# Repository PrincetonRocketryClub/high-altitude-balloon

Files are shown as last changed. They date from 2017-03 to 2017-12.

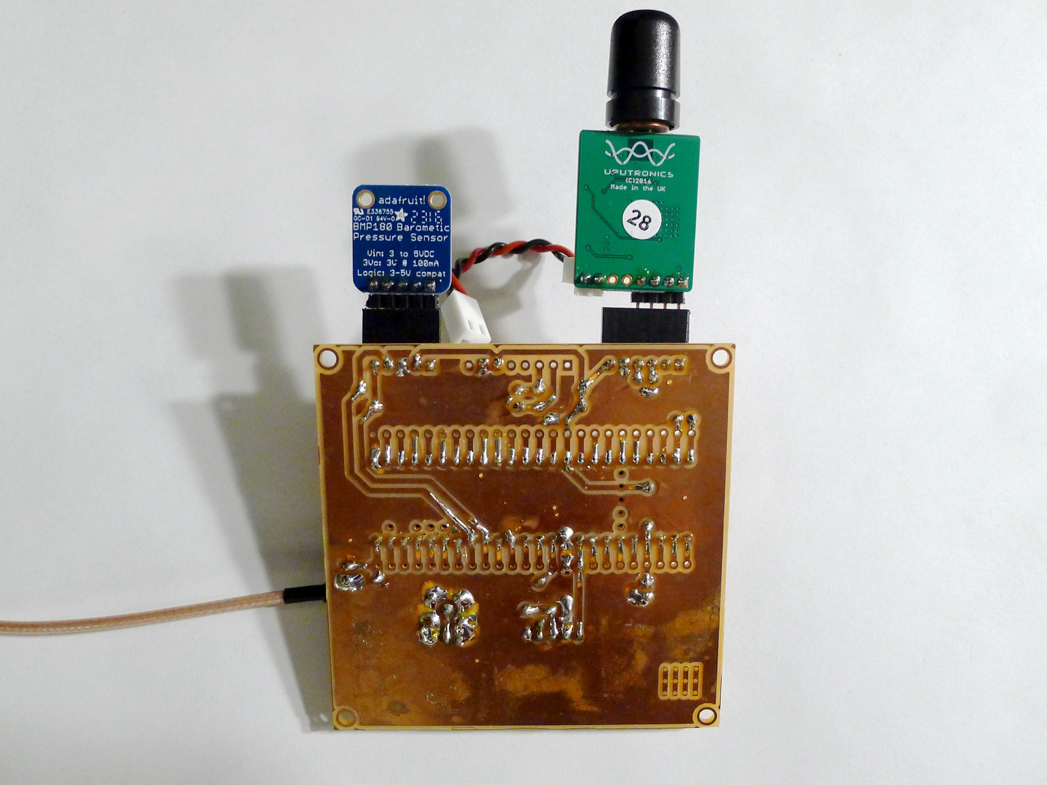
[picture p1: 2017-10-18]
images/avionics_back.jpg

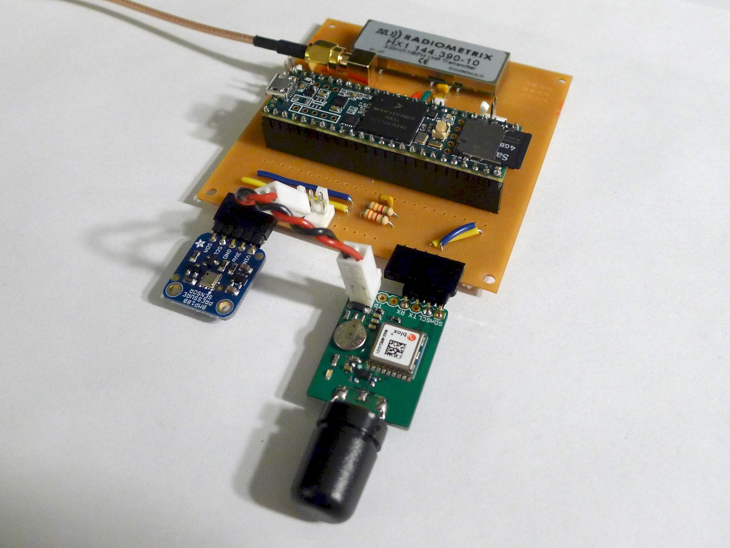
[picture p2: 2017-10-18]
images/avionics_front.jpg

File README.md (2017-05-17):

# High Altitude Balloon
High Altitude Balloon for the Global Space Balloon Challenge.

Electronics without battery is 70 grams, battery is 98 grams.

## Controller
The primary microcontroller used is a [Teensy 3.5](https://www.pjrc.com/store/teensy35.html). The Teensy is a Arduino-compatible ARM based development board. 

Software will be based on the [Trackuino project](https://github.com/trackuino/trackuino) with modifications for Teensy DAC support from [this project.](https://github.com/rvnash/aprs_teensy31)

## Communications
Telemetry will be sent via 2m APRS using the [HX1 2m Transmitter](http://www.radiometrix.com/content/hx1). This module has an output power of ~300mW tuned to a frequency of 144.390 MHz. There are reports of frequency drift with temperature, so this behavior will have to be characterized before launch.

Antenna will be a simple half-wavelength dipole, likely based on [this](http://bear.sbszoo.com/construction/antenna/cf/hwcf2.htm) or [this.](http://bear.sbszoo.com/construction/antenna/cf/hwcf1.htm)

### APRS Message Format
Use standard headers etc. Symbol `/O` (Primay symbol table, symbol ID 'O' corresponding to balloon). Message type based on "Lat/Long Position Report Format — with Data Extension and Timestamp" in the [APRS spec](http://www.aprs.org/doc/APRS101.PDF).

String:
`[Data Type ID flag:/]HHMMSSh[Latitude ddmm.hh[N/S](8b)][SymtableID (1b)][Longitude dddmm.hh[W/E](9b)][Symbol Code (1b)][Course/Speed (7b)][Arb. data (36b)]`  

### Comment format
Chars | Description | Example
----- | ----------- | -------
5 | Timestamp (sec) | 12000
1 | Separator | ,
5 | BMP180 Temperature (C) | -60.0
1 | Separator | ,
6 | BMP180 Pressure (Pa) | 101580
1 | Separator | ,
4 | Thermistor ADC Value, max 1023 | 1017
23 | Total |

### HX-1 Transmitter
- [Main Page](http://www.radiometrix.com/content/hx1)

Pinout

Pin Label | Functionality | Connection
--------- | ------------- | ----------
1, 3 | RF Ground | SMA Shield
2 | RF out | SMA Center pin
4 | Active-high Enable | Digital pin 11
5 | 5V Supply | N/A
6 | GND | N/A
7 | TX Data | DAC1

# Sensors
## U-Blox MAX-M8 GPS Receiver
### Datasheets
- [Breakout Board](https://store.uputronics.com/?route=product/product&product_id=72)
- [Hardware Specs](https://www.u-blox.com/sites/default/files/MAX-M8-FW3_DataSheet_%28UBX-15031506%29.pdf)
- [Protocol Spec](https://www.u-blox.com/sites/default/files/products/documents/u-blox8-M8_ReceiverDescrProtSpec_%28UBX-13003221%29_Public.pdf)

### Software
Outputs NEMA strings over serial, so should integrate with Trackuino's code nicely. Might have to do some configuration via UART. See page 175 of protocol spec for NMEA config. 

Config example code: http://playground.arduino.cc/UBlox/GPS
Other tutorial: http://ava.upuaut.net/?p=738

The settings we'll need:
- Set non-GPS source's ID's to GPGGA for compatibility
- Double check all available sources are enabled
- Disable some unnecessary debug outputs
- Figure out how to switch between low and high altitude mode
- Change refresh rate

### I/O
Pin Label | Functionality | Connection
--------- | ------------- | ----------
SDA | I2C | N/A
SCL | I2C | N/A 
TXD | Serial UART | Serial4 RX
RXD | Serial UART | Serial4 TX
GND | Ground | 
VCC | 3.3V Power | 

## BMP180 Barometer/Temperature
### Datasheets
- [Adafruit](https://www.adafruit.com/products/1603)
- [Library](https://learn.sparkfun.com/tutorials/bmp180-barometric-pressure-sensor-hookup-/installing-the-arduino-library)

### Software
Use the Sparkfun library. Communicates over I2C, nothing fancy. Must use SCL/SDA0 since those correspond to the default Wire interface.

### I/O
Pin Label | Functionality | Connection
--------- | ------------- | ----------
VIN | 5V power in, feeds on-board regulator | N/A
3V3 | 3V3 power rail | N/A 
GND | Ground | Black
SCL | I2C | SCL0 (Pin 19)
SDA | I2C | SDA0 (Pin 18)

## MMA8451 3-axis accelerometer
### Datasheets
- [Adafruit](https://www.adafruit.com/product/2019)
- [Library](https://learn.adafruit.com/adafruit-mma8451-accelerometer-breakout/wiring-and-test)

### Software
Use the Adafruit library. Communicates over I2C.

### I/O
Pin Label | Functionality | Wire Color
--------- | ------------- | ----------
VIN | 5V power in, feeds on-board regulator | NC
3Vo | 3V3 power rail | N/A 
GND | Ground | Black
SCL | I2C | SCL0 (Pin 19)
SDA | I2C | SDA0 (Pin 18)
A | Address Select | NC for address 0x1C
I1 | Interrupt 1 | NC
I2 | Interrupt 2 | NC

## 3950 NTC Thermristor
### Datasheets
- [Adafruit](https://www.adafruit.com/product/372)
- [Tutorial](https://learn.adafruit.com/thermistor/using-a-thermistor)
- [Lookup Table](https://cdn-shop.adafruit.com/datasheets/103_3950_lookuptable.pdf)

Hook it up with a 10k resistor in a voltage divider setup, read with ADC. Connected to ADC17

# Actuators

## Electric heating pad

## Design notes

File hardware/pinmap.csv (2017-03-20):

Teensy Pin | Configuration | Connected To | Wire Color
0
1
2
3
4
5
6
7
8
9
10
11 | Digital Out | HX1 Transmitter Enable
12
13
14
15
16 | SDA0 | Accelerometer, Barometer I2C
17 | SCL0 | Accelerometer, Barometer I2C
18
19
20
21
22
23
24
25
26
27
28
29
30
31 | Serial4 RX | GPS TX
32 | Serial4 TX | GPS RX
33
34 | Analog In 17 | Thermistor
35
36
37
38
39
DAC0
DAC1 |  | HX1 Transmitter Signal

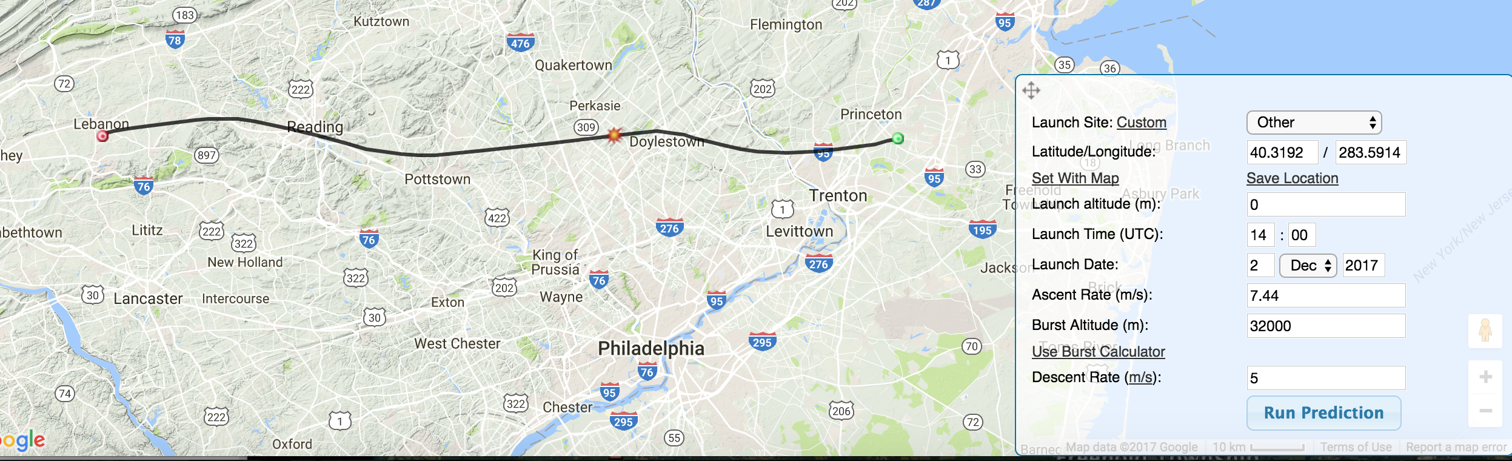
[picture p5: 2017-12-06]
records/Screen Shot 2017-12-01 at 11.11.32 PM.png

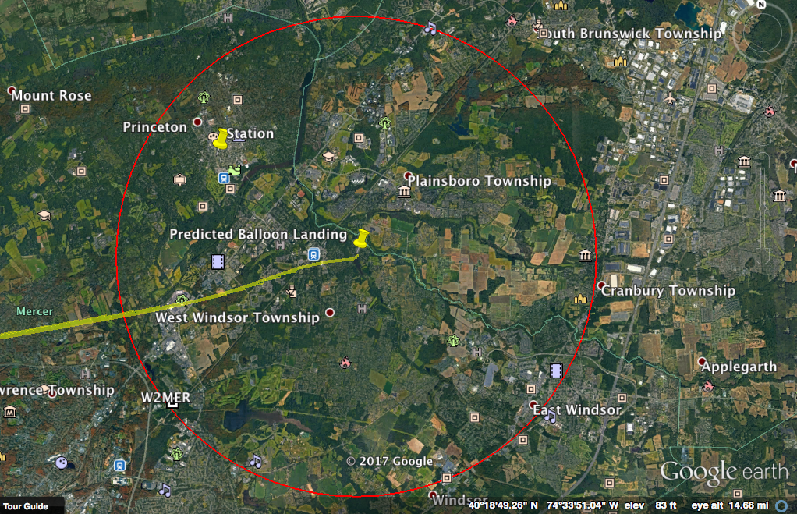
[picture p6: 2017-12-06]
records/Screen Shot 2017-12-01 at 11.14.21 PM.png

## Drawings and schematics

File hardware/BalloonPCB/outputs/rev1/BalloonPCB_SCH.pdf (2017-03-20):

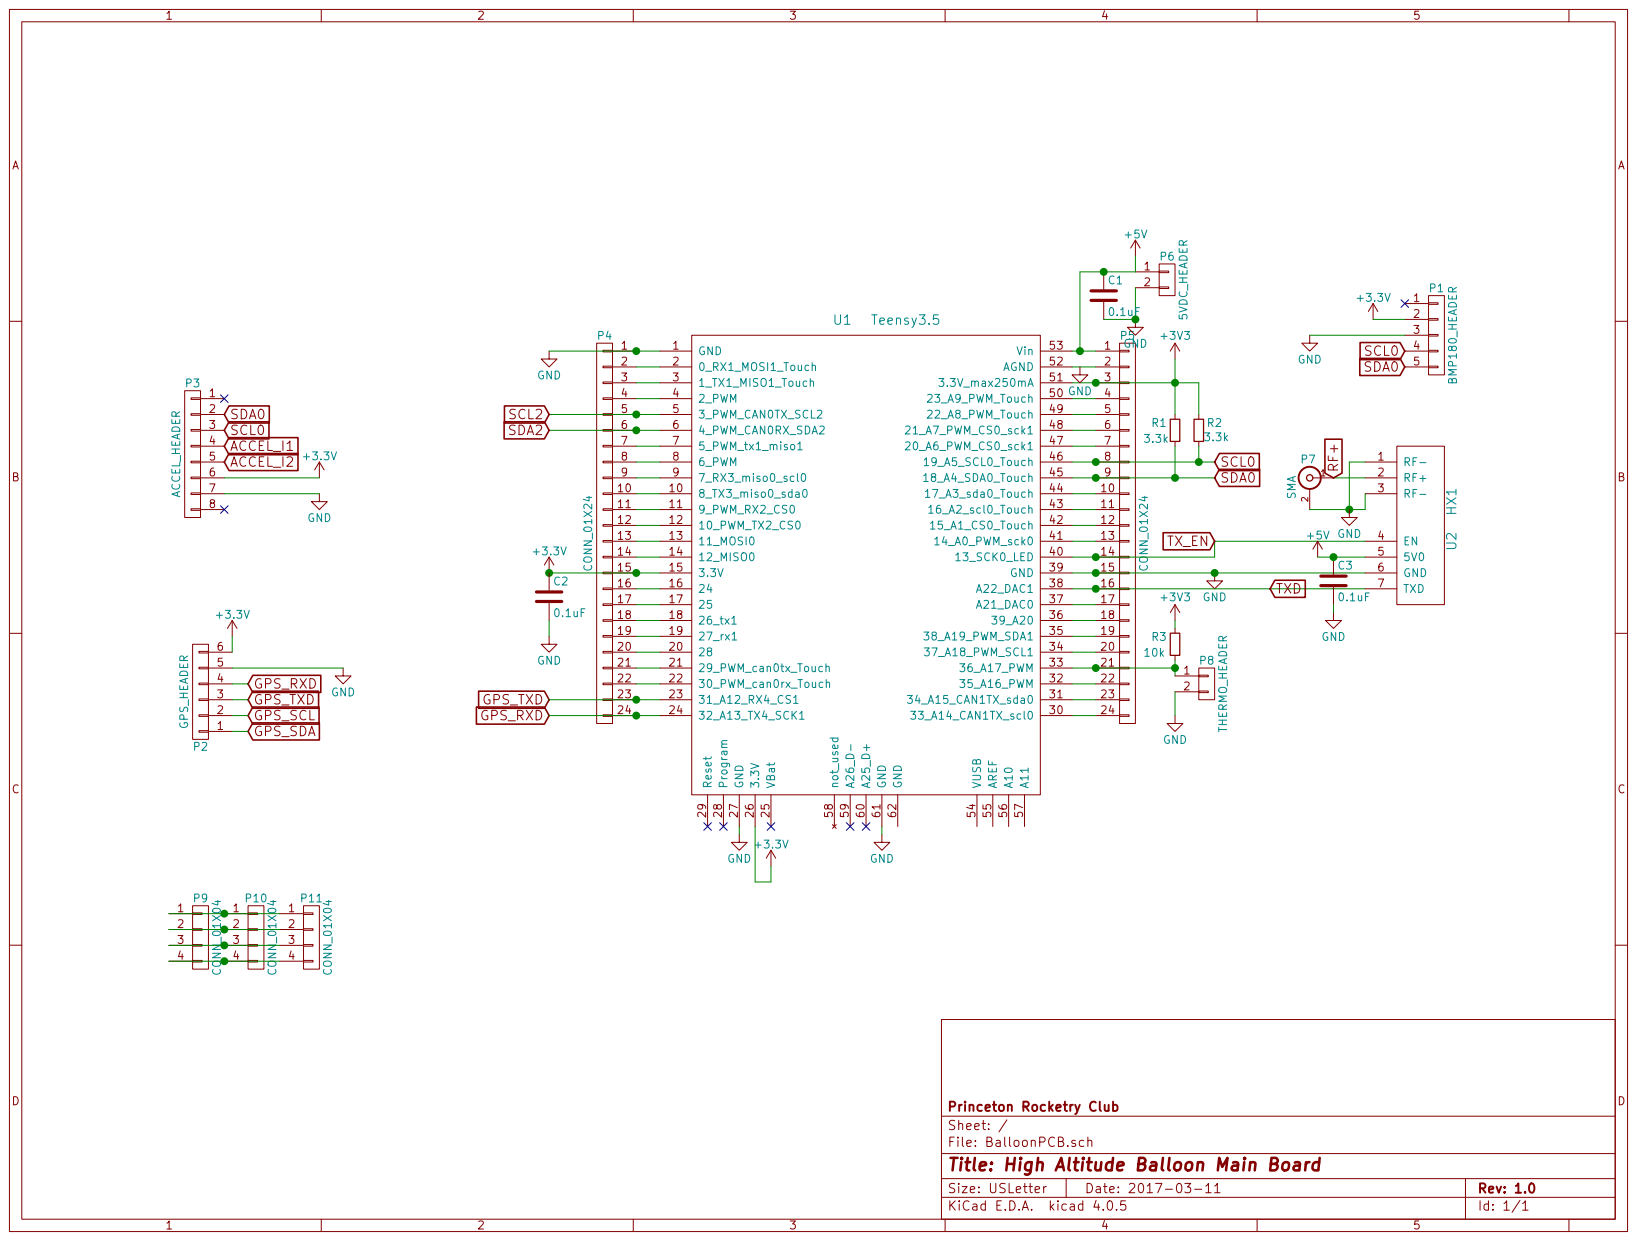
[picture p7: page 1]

2 3 4 5 | 0_RX1_MOSI1_Touch 2 1_TX1_MISO1_Touch 3 2_PWM 4 3_PWM_CAN0TX_SCL2 5 | 2

GND 4

6 | 4_PWM_CAN0RX_SDA2 6 | 6
7 8 9 10 11 12 13 14 15 | 5_PWM_tx1_miso1 7 6_PWM 8 7_RX3_miso0_scl0 9 8_TX3_miso0_sda0 10 9_PWM_RX2_CS0 11 10_PWM_TX2_CS0 12 11_MOSI0 13 12_MISO0 14 3.3V 15 | 7

12
13

16 17 18 19 20 21 22 23 | 24 16 25 17 28 20 29_PWM_can0tx_Touch 21 31_A12_RX4_CS1 23 | 16

17
18
19
20

22
23

24 | 32_A13_TX4_SCK1 24 | 24

Princeton Rocketry Club
Sheet: /
File: BalloonPCB.sch
Title: High Altitude Balloon Main Board

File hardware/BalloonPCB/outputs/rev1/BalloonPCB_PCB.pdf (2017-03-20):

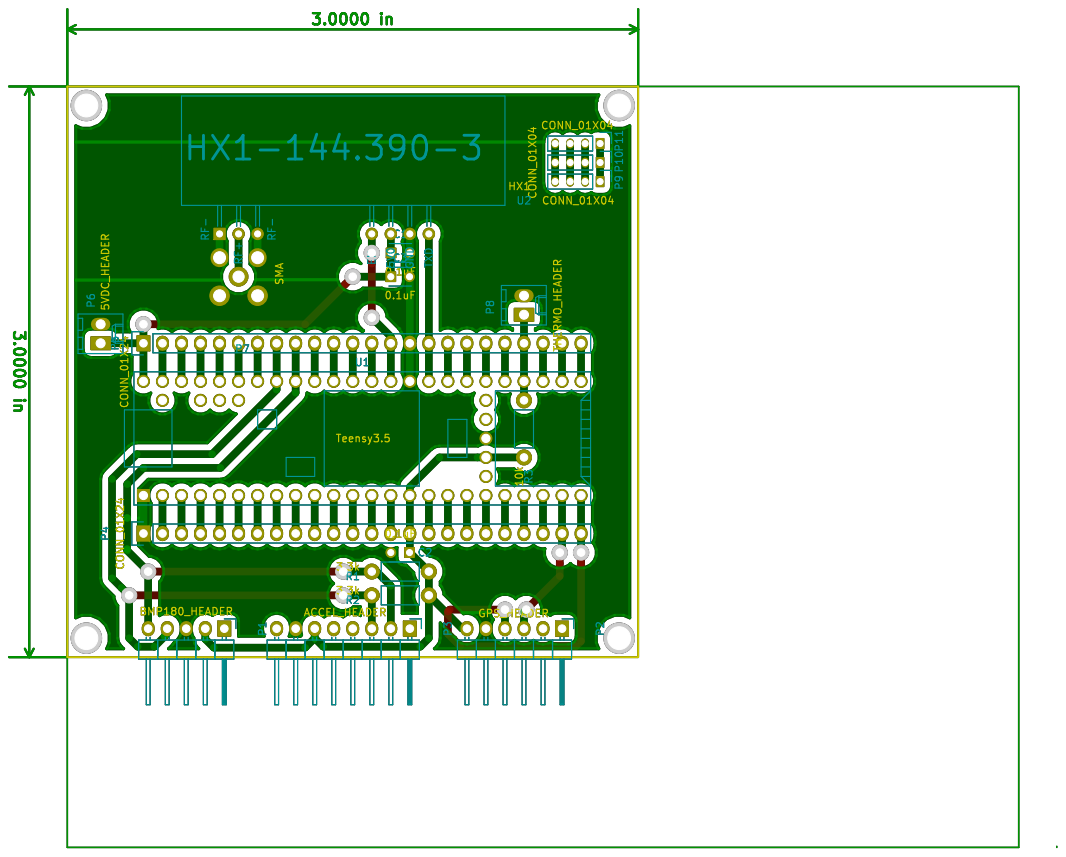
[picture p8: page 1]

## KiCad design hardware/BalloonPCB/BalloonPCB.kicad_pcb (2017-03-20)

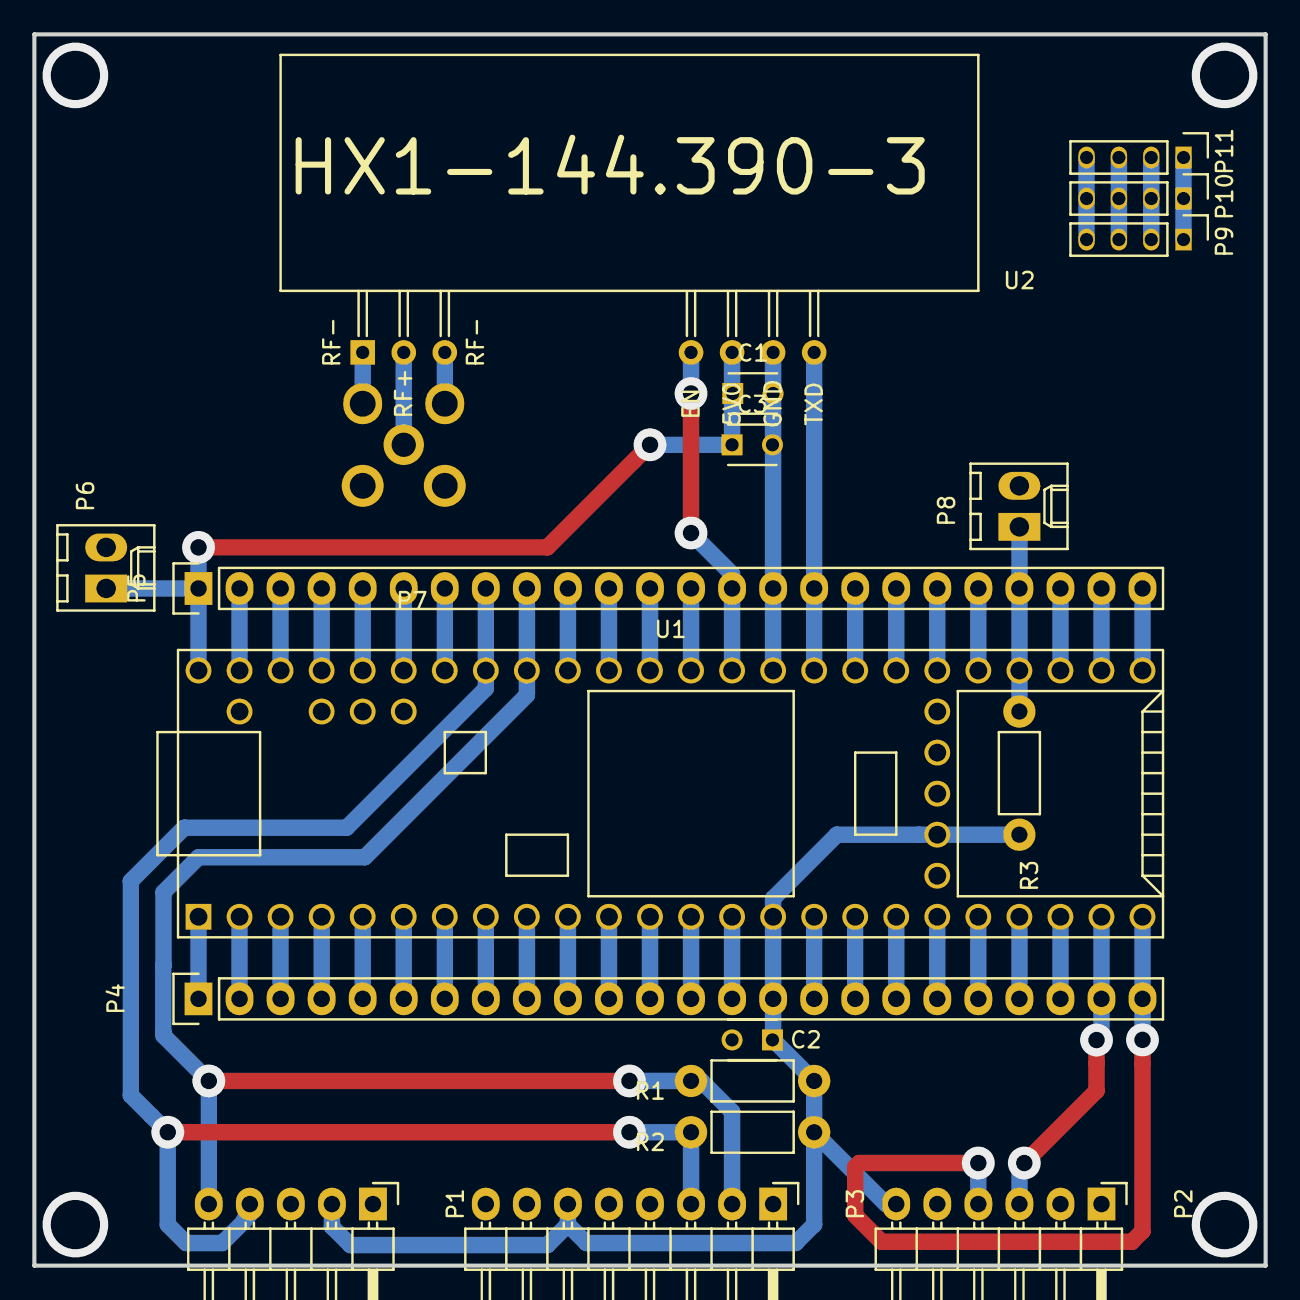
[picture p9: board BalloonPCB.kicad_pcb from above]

Board: 2 copper layers, 76.2 x 76.2 mm, 19 parts (0 on the bottom side), 51 nets.

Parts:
C1, C2, C3: 0.1uF; C_Disc_D3_P2.5
P1: BMP180_HEADER; Pin_Header_Angled_1x05
P2: GPS_HEADER; Pin_Header_Angled_1x06
P3: ACCEL_HEADER; Pin_Header_Angled_1x08
P4, P5: CONN_01X24; Pin_Header_Straight_1x24
P6: 5VDC_HEADER; Molex_KK-6410-02_02x2.54mm_Straight
P7: SMA; SMA_Socket_TYCO-AMP
P8: THERMO_HEADER; Molex_KK-6410-02_02x2.54mm_Straight
P9, P10, P11: CONN_01X04; Pin_Header_Straight_1x04_Pitch2.00mm
R1, R2: 3.3k; Resistor_Horizontal_RM7mm
R3: 10k; Resistor_Horizontal_RM7mm
U1: Teensy3.5; Teensy35_36
U2: HX1

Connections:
+3V3: C2.1, P1.2, P2.6, P3.6, P4.15, P5.3, R1.1, R2.1, R3.1, U1.15, U1.26, U1.51
+5V: C1.1, C3.1, P5.1, P6.1, U1.53, U2.5
GND: C1.2, C2.2, C3.2, P1.3, P2.5, P3.7, P4.1, P5.15, P6.2, P7.2, P8.2, U1.1, U1.27, U1.39, U2.1, U2.3, U2.6
GPS_RXD: P2.4, P4.24, U1.24
GPS_TXD: P2.3, P4.23, U1.23
unnamed: P4.2, U1.2
unnamed: P4.3, U1.3
unnamed: P4.4, U1.4
unnamed: P4.7, U1.7
unnamed: P4.8, U1.8
unnamed: P4.9, U1.9
unnamed: P4.10, U1.10
unnamed: P4.11, U1.11
unnamed: P4.12, U1.12
unnamed: P4.13, U1.13
unnamed: P4.14, U1.14
unnamed: P4.16, U1.16
unnamed: P4.17, U1.17
unnamed: P4.18, U1.18
unnamed: P4.19, U1.19
unnamed: P4.20, U1.20
unnamed: P4.21, U1.21
unnamed: P4.22, U1.22
unnamed: P5.2, U1.52
unnamed: P5.4, U1.50
unnamed: P5.5, U1.49
unnamed: P5.6, U1.48
unnamed: P5.7, U1.47
unnamed: P5.10, U1.44
unnamed: P5.11, U1.43
unnamed: P5.12, U1.42
unnamed: P5.13, U1.41
unnamed: P5.17, U1.37
unnamed: P5.18, U1.36
unnamed: P5.19, U1.35
unnamed: P5.20, U1.34
unnamed: P5.21, P8.1, R3.2, U1.33
unnamed: P5.22, U1.32
unnamed: P5.23, U1.31
unnamed: P5.24, U1.30
unnamed: P9.1, P10.1, P11.1
unnamed: P9.2, P10.2, P11.2
unnamed: P9.3, P10.3, P11.3
unnamed: P9.4, P10.4, P11.4
RF+: P7.1, U2.2
SCL0: P1.4, P3.3, P5.8, R2.2, U1.46
SCL2: P4.5, U1.5
SDA0: P1.5, P3.2, P5.9, R1.2, U1.45
SDA2: P4.6, U1.6
TXD: P5.16, U1.38, U2.7
TX_EN: P5.14, U1.40, U2.4

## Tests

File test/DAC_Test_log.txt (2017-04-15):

19:00:27$ fm AG6GR-11 to APRS-0 via WIDE1-1,WIDE2-2 UI  PID=F0
          /123519h4802.74N/01100.93E0000/000/A=001789HELLO
19:00:30$ fm AG6GR-11 to APRS-0 via WIDE1-1,WIDE2-2 UI  PID=F0
          /123519h4802.74N/01100.93E0000/000/A=001789HELLO
19:00:32$ fm AG6GR-11 to APRS-0 via WIDE1-1,WIDE2-2 UI  PID=F0
          /123519h4802.74N/01100.93E0000/000/A=001789HELLO
19:00:34$ fm AG6GR-11 to APRS-0 via WIDE1-1,WIDE2-2 UI  PID=F0
          /123519h4802.74N/01100.93E0000/000/A=001789HELLO
19:00:36$ fm AG6GR-11 to APRS-0 via WIDE1-1,WIDE2-2 UI  PID=F0
          /123519h4802.74N/01100.93E0000/000/A=001789HELLO
19:00:38$ fm AG6GR-11 to APRS-0 via WIDE1-1,WIDE2-2 UI  PID=F0
          /123519h4802.74N/01100.93E0000/000/A=001789HELLO
19:00:40$ fm AG6GR-11 to APRS-0 via WIDE1-1,WIDE2-2 UI  PID=F0
          /123519h4802.74N/01100.93E0000/000/A=001789HELLO
19:00:42$ fm AG6GR-11 to APRS-0 via WIDE1-1,WIDE2-2 UI  PID=F0
          /123519h4802.74N/01100.93E0000/000/A=001789HELLO
19:00:44$ fm AG6GR-11 to APRS-0 via WIDE1-1,WIDE2-2 UI  PID=F0
          /123519h4802.74N/01100.93E0000/000/A=001789HELLO
19:00:46$ fm AG6GR-11 to APRS-0 via WIDE1-1,WIDE2-2 UI  PID=F0
          /123519h4802.74N/01100.93E0000/000/A=001789HELLO
19:00:50$ fm AG6GR-11 to APRS-0 via WIDE1-1,WIDE2-2 UI  PID=F0
          /123519h4802.74N/01100.93E0000/000/A=001789HELLO
19:00:52$ fm AG6GR-11 to APRS-0 via WIDE1-1,WIDE2-2 UI  PID=F0
          /123519h4802.74N/01100.93E0000/000/A=001789HELLO
19:00:54$ fm AG6GR-11 to APRS-0 via WIDE1-1,WIDE2-2 UI  PID=F0
          /123519h4802.74N/01100.93E0000/000/A=001789HELLO
19:00:57$ fm AG6GR-11 to APRS-0 via WIDE1-1,WIDE2-2 UI  PID=F0
          /123519h4802.74N/01100.93E0000/000/A=001789HELLO
19:00:59$ fm AG6GR-11 to APRS-0 via WIDE1-1,WIDE2-2 UI  PID=F0
          /123519h4802.74N/01100.93E0000/000/A=001789HELLO
19:01:01$ fm AG6GR-11 to APRS-0 via WIDE1-1,WIDE2-2 UI  PID=F0
          /123519h4802.74N/01100.93E0000/000/A=001789HELLO
19:01:03$ fm AG6GR-11 to APRS-0 via WIDE1-1,WIDE2-2 UI  PID=F0
          /123519h4802.74N/01100.93E0000/000/A=001789HELLO
19:01:05$ fm AG6GR-11 to APRS-0 via WIDE1-1,WIDE2-2 UI  PID=F0
          /123519h4802.74N/01100.93E0000/000/A=001789HELLO
19:01:07$ fm AG6GR-11 to APRS-0 via WIDE1-1,WIDE2-2 UI  PID=F0
          /123519h4802.74N/01100.93E0000/000/A=001789HELLO
19:01:09$ fm AG6GR-11 to APRS-0 via WIDE1-1,WIDE2-2 UI  PID=F0
          /123519h4802.74N/01100.93E0000/000/A=001789HELLO
19:01:11$ fm AG6GR-11 to APRS-0 via WIDE1-1,WIDE2-2 UI  PID=F0
          /123519h4802.74N/01100.93E0000/000/A=001789HELLO
19:01:13$ fm AG6GR-11 to APRS-0 via WIDE1-1,WIDE2-2 UI  PID=F0
          /123519h4802.74N/01100.93E0000/000/A=001789HELLO
19:01:15$ fm AG6GR-11 to APRS-0 via WIDE1-1,WIDE2-2 UI  PID=F0
          /123519h4802.74N/01100.93E0000/000/A=001789HELLO
19:01:17$ fm AG6GR-11 to APRS-0 via WIDE1-1,WIDE2-2 UI  PID=F0
          /123519h4802.74N/01100.93E0000/000/A=001789HELLO
19:01:19$ fm AG6GR-11 to APRS-0 via WIDE1-1,WIDE2-2 UI  PID=F0
          /123519h4802.74N/01100.93E0000/000/A=001789HELLO
19:01:21$ fm AG6GR-11 to APRS-0 via WIDE1-1,WIDE2-2 UI  PID=F0
          /123519h4802.74N/01100.93E0000/000/A=001789HELLO
19:01:24$ fm AG6GR-11 to APRS-0 via WIDE1-1,WIDE2-2 UI  PID=F0
          /123519h4802.74N/01100.93E0000/000/A=001789HELLO
19:01:26$ fm AG6GR-11 to APRS-0 via WIDE1-1,WIDE2-2 UI  PID=F0
          /123519h4802.74N/01100.93E0000/000/A=001789HELLO
19:01:28$ fm AG6GR-11 to APRS-0 via WIDE1-1,WIDE2-2 UI  PID=F0
          /123519h4802.74N/01100.93E0000/000/A=001789HELLO
19:01:30$ fm AG6GR-11 to APRS-0 via WIDE1-1,WIDE2-2 UI  PID=F0
          /123519h4802.74N/01100.93E0000/000/A=001789HELLO
19:01:32$ fm AG6GR-11 to APRS-0 via WIDE1-1,WIDE2-2 UI  PID=F0
          /123519h4802.74N/01100.93E0000/000/A=001789HELLO
19:01:34$ fm AG6GR-11 to APRS-0 via WIDE1-1,WIDE2-2 UI  PID=F0
          /123519h4802.74N/01100.93E0000/000/A=001789HELLO
19:01:36$ fm AG6GR-11 to APRS-0 via WIDE1-1,WIDE2-2 UI  PID=F0
          /123519h4802.74N/01100.93E0000/000/A=001789HELLO
19:01:38$ fm AG6GR-11 to APRS-0 via WIDE1-1,WIDE2-2 UI  PID=F0
          /123519h4802.74N/01100.93E0000/000/A=001789HELLO
19:01:40$ fm AG6GR-11 to APRS-0 via WIDE1-1,WIDE2-2 UI  PID=F0
          /123519h4802.74N/01100.93E0000/000/A=001789HELLO
19:01:42$ fm AG6GR-11 to APRS-0 via WIDE1-1,WIDE2-2 UI  PID=F0
          /123519h4802.74N/01100.93E0000/000/A=001789HELLO
19:01:44$ fm AG6GR-11 to APRS-0 via WIDE1-1,WIDE2-2 UI  PID=F0
          /123519h4802.74N/01100.93E0000/000/A=001789HELLO
19:01:46$ fm AG6GR-11 to APRS-0 via WIDE1-1,WIDE2-2 UI  PID=F0
          /123519h4802.74N/01100.93E0000/000/A=001789HELLO

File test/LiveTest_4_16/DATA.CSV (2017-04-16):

Timestamp (ms) | Time | Latitude | Longitude | Altitude (cm) | BMP180 Temperature | BMP180 Pressure | Thermistor
2188 | 0 | 0.000000 | 0.000000 | 0 | 28.4 | 100191 | 462
4357 | 0 | 0.000000 | 0.000000 | 0 | 29.0 | 100239 | 460
6526 | 0 | 0.000000 | 0.000000 | 0 | 29.5 | 100233 | 458
8697 | 0 | 0.000000 | 0.000000 | 0 | 29.9 | 100236 | 455
10812 | 0 | 0.000000 | 0.000000 | 0 | 30.3 | 100242 | 451
12899 | 0 | 0.000000 | 0.000000 | 0 | 30.6 | 100235 | 448
14984 | 0 | 0.000000 | 0.000000 | 0 | 30.9 | 100233 | 445
17070 | 0 | 0.000000 | 0.000000 | 0 | 31.3 | 100226 | 441
19156 | 0 | 0.000000 | 0.000000 | 0 | 31.7 | 100242 | 435
21242 | 0 | 0.000000 | 0.000000 | 0 | 32.1 | 100233 | 431
23329 | 0 | 0.000000 | 0.000000 | 0 | 32.4 | 100245 | 428
25415 | 0 | 0.000000 | 0.000000 | 0 | 32.6 | 100242 | 424
27501 | 0 | 0.000000 | 0.000000 | 0 | 32.9 | 100236 | 421
29587 | 0 | 0.000000 | 0.000000 | 0 | 33.1 | 100244 | 418
31673 | 0 | 0.000000 | 0.000000 | 0 | 33.2 | 100252 | 416
33770 | 0 | 0.000000 | 0.000000 | 0 | 33.5 | 100247 | 414
35870 | 0 | 0.000000 | 0.000000 | 0 | 33.8 | 100248 | 411
37956 | 0 | 0.000000 | 0.000000 | 0 | 33.9 | 100237 | 410
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

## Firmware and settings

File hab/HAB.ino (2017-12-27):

/*
* Copyright (C) 2017 by Sunny He (AG6GR)
* 
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
* You should have received a copy of the GNU General Public License
* along with this program; if not, write to the Free Software
* Foundation, Inc., 51 Franklin Street, Fifth Floor, Boston, MA  02110-1301, USA.
*/

#include <WProgram.h>
#include <SD.h>
#include <SPI.h>

#include "aprs.h"

// Ublox configuration code
#include "ublox.h"

// TinyGPSPlus from http://arduiniana.org/libraries/tinygpsplus/
#include "TinyGPS.h"
// Adafruit BMP180 Library
#include "adafruit_BMP085.h"

// ----- Pin Definitions ----- //
#define PTT_PIN 13 // Push to talk pin
#define THERMISTOR_PIN 36 // Thermistor Analog Input
#define VALVE_PIN 33

#define GPS_SERIAL Serial4 // GPS Serial port
#define GPS_BAUDRATE 9600

// ----- APRS Constants ----- //
// Callsign and SSID
#define S_CALLSIGN "AG6GR"
#define S_CALLSIGN_ID	11	 //  SSID is the attached ID number ex. W1AW-11. 11 is usually for balloons

// Destination callsign: APRS (with SSID=0) is usually okay.
#define D_CALLSIGN		"APRS"
#define D_CALLSIGN_ID	0

// Symbol Table: '/' is primary table '\' is secondary table
#define SYMBOL_TABLE '/' 
// Primary Table Symbols: /O=balloon, /-=House, /v=Blue Van, />=Red Car
#define SYMBOL_CHAR 'O'

// ----- Misc Constants ----- //
#define MAXSENDBUFFER 500 // Used to allocate a static buffer on the stack to build the AX25 buffer
#define LOGGINGPERIOD 2000
#define LOGGINGFILENAME "data.csv"
#define SAMPLE_ALTITUDE 20000


// ===== GLOBAL VARIABLES ==== //
char strbuf[MAXSENDBUFFER] = {};

struct PathAddress addresses[] = {
	{(char *)D_CALLSIGN, D_CALLSIGN_ID},	// Destination callsign
	{(char *)S_CALLSIGN, S_CALLSIGN_ID},	// Source callsign
	{(char *)NULL, 0}, // Digi1 (first digi in the chain)
	{(char *)NULL, 0}	 // Digi2 (second digi in the chain)
};

TinyGPSPlus gps; // GPS NEMA string decoder
Adafruit_BMP085 bmp180; // BMP180 Temperature/Pressure sensor

uint32_t timeOfAPRS = 0; // Time of last APRS transmission
uint32_t timeLogging = 0; // Time of last logging output
ublox_navmode_t currentUbloxMode = NAVMODE_LOW_PORTABLE;
uint16_t APRS_period = 60000;

char hasSampled = 0;
// ===== FUNCTIONS ===== //

/*
 * Sets up and transmits a APRS packet, using the given GPS instance and
 * comment string
 */
void broadcastLocation(TinyGPSPlus &gps, char *comment)
{
	int nAddresses;
	if (gps.altitude.meters() > 1500) {
		// APRS recomendations for > 5000 feet = 1500 m is:
		// Path: WIDE2-1 is acceptable, but no path is preferred.
		nAddresses = 3;
		addresses[2].callsign = "WIDE2";
		addresses[2].ssid = 1;
	} else {
		// Below 1500 meters use a much more generous path (assuming a mobile station)
		// Path is "WIDE1-1,WIDE2-2"
		nAddresses = 4;
		addresses[2].callsign = "WIDE1";
		addresses[2].ssid = 1;
		addresses[3].callsign = "WIDE2";
		addresses[3].ssid = 2;
	}
	
	// For debugging print out the path
	
	Serial.print("APRS(");
	Serial.print(nAddresses);
	Serial.print("): ");
	for (int i=0; i < nAddresses; i++) {
		Serial.print(addresses[i].callsign);
		Serial.print('-');
		Serial.print(addresses[i].ssid);
		if (i < nAddresses-1)
			Serial.print(',');
	}
	Serial.print(' ');
	Serial.print(SYMBOL_TABLE);
	Serial.print(SYMBOL_CHAR);
	Serial.println();
	
	
	// Package the packet
	createAPRSStr(strbuf, gps, SYMBOL_TABLE, SYMBOL_CHAR, comment);
	
	// Send the packet
	aprs_send(addresses, nAddresses, strbuf);
}

// ----- Setup Code (Run on Startup) ----- //
void setup()
{
	Serial.begin(19200); // For debugging output over the USB port
	Serial.println("Starting...");
	
	// ----- GPS Setup ----- //
	Serial.println("----- GPS SETUP -----");
	GPS_SERIAL.begin(GPS_BAUDRATE);
	
	Serial.println("Configuring NEMA talker ID to GP");
	sendConfig(UBLOX_SET_NMEA_TALKER_GP, UBLOX_SET_NMEA_TALKER_GP_LEN);
	
	while (ublox_setRate(2000) == -1){
		Serial.println("Checksum mismatch, retrying...");
	}
	while (ublox_setNavMode(NAVMODE_LOW_PORTABLE) == -1){
		Serial.println("Checksum mismatch, retrying...");
	}
	
	// ----- BMP180 Setup ----- //
	Serial.println("----- BMP180 SETUP -----");
	if (bmp180.begin()) {
		Serial.println("BMP180 Setup Successful");
	} else {
		Serial.println("BMP180 Not Found");
	}
	
	// ----- APRS Setup ----- //
	Serial.println("----- APRS SETUP -----");
	aprs_setup(50, // number of preamble flags to send
		PTT_PIN, // Use PTT pin
		100, // ms to wait after PTT to transmit
		0, 0 // No VOX ton
	);
	
	// ----- SD Setup ----- //
	Serial.println("----- SD SETUP -----");
	if (SD.begin(BUILTIN_SDCARD)) {
		Serial.println("SD init succesful");
	} else {
		Serial.println("SD init failed, or card not present");
	}
	
	if (SD.exists(LOGGINGFILENAME)) {
		Serial.print(LOGGINGFILENAME);
		Serial.println(" already exists");
	} else {
		Serial.print(LOGGINGFILENAME);
		Serial.println(" not found, creating");
		File dataFile = SD.open(LOGGINGFILENAME, FILE_WRITE);
		dataFile.println("Timestamp (ms), Time, Latitude, Longitude, Altitude (cm), BMP180 Temperature, BMP180 Pressure, Thermistor");
		dataFile.close();
	}
	
	Serial.println("===== SETUP COMPLETE =====");
	
	// ----- Test REMOVE BEFORE LAUNCH ----- //
	/*
	char* test_gps = "$GPGGA,123519,4807.038,N,01131.000,E,1,08,0.9,545.4,M,46.9,M,,*47\n";
	for (int i = 0; i < 67; i++)
		gps.encode(test_gps[i]);
	*/
}

// -----  Main loop (run repeatedly) ----- //
void loop()
{
	// Read in new GPS data if available
	while (GPS_SERIAL.available() > 0) {
		char readbyte = GPS_SERIAL.read();
		Serial.print(readbyte);
		gps.encode(readbyte);
	}
	
	// Debug: Also read from USB Serial
	while (Serial.available() > 0)
		gps.encode(Serial.read());
	
	// GPS Debug logging
	if ((gps.location.isUpdated() || gps.satellites.isUpdated()) && gps.time.value() != 0) {
		Serial.printf("\r\nGPS Update %d:%d:%d T=+%ul\r\n", 
			gps.time.hour(), gps.time.minute(), gps.time.second(), millis());
		Serial.printf("Location: %f, %f altitude %f\r\n",
			gps.location.lat(), gps.location.lng(), gps.altitude.meters());
		Serial.printf("Satellites: %d\r\n", gps.satellites.value());
	} else {
		/*
		Serial.print("No GPS ");
		Serial.println(gps.charsProcessed());
		Serial.print("Pass: ");
		Serial.print(gps.passedChecksum());
		Serial.print(" Fail: ");
		Serial.println(gps.failedChecksum());
		Serial.printf("Location: %f, %f altitude %f\r\n",
			gps.location.lat(), gps.location.lng(), gps.altitude.meters());
		*/
	}
	if (gps.altitude.isValid()) {
		if (gps.altitude.meters() > 100 && currentUbloxMode != NAVMODE_AIRBORNE_1G) {
			ublox_setNavMode(NAVMODE_AIRBORNE_1G);
			currentUbloxMode = NAVMODE_AIRBORNE_1G;
		} else if(gps.altitude.meters() < 100 && currentUbloxMode != NAVMODE_LOW_PORTABLE) {
			ublox_setNavMode(NAVMODE_LOW_PORTABLE);
			currentUbloxMode = NAVMODE_LOW_PORTABLE;
		}
	}
	
	if (gps.location.isValid() && millis() - timeOfAPRS > APRS_period) {
		Serial.println("===== APRS Transmission =====");
		char comment[36];
		snprintf(comment, 36, "%lu,%.1fC,%lu,%d", 
			millis()/1000,
			bmp180.readTemperature(), 
			bmp180.readPressure(), 
			analogRead(THERMISTOR_PIN));
		
		broadcastLocation(gps, comment);
		timeOfAPRS = millis();
		
		if (gps.altitude.isValid() && gps.altitude.meters() > 500) {
			APRS_period = 120000;
		} else {
			APRS_period = 60000;
		}
	}
	
	if (millis() - timeLogging > LOGGINGPERIOD) {
		Serial.printf("Logging T = +%lu\r\n", millis()/1000);
		Serial.printf("Temperature: %.1fC, Pressure %d Pa\r\n", 
			bmp180.readTemperature(), bmp180.readPressure());
		Serial.print("Thermistor ADC: ");
		Serial.println(analogRead(THERMISTOR_PIN));
		Serial.print("Air sample: ");
		Serial.print(hasSampled);
		
		File dataFile = SD.open(LOGGINGFILENAME, FILE_WRITE);
		if (dataFile) {
			dataFile.printf("%lu,%lu,%f,%f,%lu,%.1f,%lu,%d,%d\r\n",
				millis(),
				gps.time.value(),
				gps.location.lat(),
				gps.location.lng(),
				gps.altitude.value(),
				bmp180.readTemperature(),
				bmp180.readPressure(),
				analogRead(THERMISTOR_PIN),
				hasSampled
			);
			dataFile.close();
		} else {
			Serial.print("Error opening ");
			Serial.println(LOGGINGFILENAME);
		}
		timeLogging = millis();
		
		// Air sampling
		if (hasSampled == 0 && altitude > SAMPLE_ALTITUDE) {
			digitalWrite(VALVE_PIN, HIGH);
			hasSampled = 1;
		} else {
			digitalWrite(VALVE_PIN, LOW);
		}
	}
}

// OLD CODE, MIGHT BE REMOVABLE Called from the powerup interrupt servicing routine.
int main(void)
{
	setup();
	while (true) {
		loop();
		yield();
	}
	return 0; // Never reached.
}

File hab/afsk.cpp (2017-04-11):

/*
 * Copyright (C) 2014 by KC3ARY Rich Nash
 * 
 * Module modified code from EA5HAV.
 *
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
 */

#include <WProgram.h>
#include "afsk.h"

// Timing constants
// All of the calculations are done in the precompiler in float point, and then
// converted to fixed point at the end (scaled up by FIXED_PNT_SCALE)

#define SAMPLES_PER_CYCLE 512 // How many samples in our sin-wave table

#define INTERRUPT_RATE 8  // in Microseconds
#define PLAYBACK_RATE (1000000.0f / INTERRUPT_RATE)     // In Hertz
#define DAC_PIN A22

// 1200 Baud settings
#define BAUD_RATE 1200.0f
#define MARK_FREQUENCY 1200.0f
#define SPACE_FREQUENCY 2200.0f
#define TONE_FREQUENCY 300.0f

// How many samples to send from the sin table for each bit
// This is a potential source of output timing drift, as this isn't very precise
// at low INTERRUPT_RATEs
// At 16 microseconds it is off by 0.1%
#define SAMPLE_COUNTER_SCALE 1000  // Increase the resolution of the sample counter
#define SAMPLES_PER_BIT_SCALED (int32_t)(SAMPLE_COUNTER_SCALE * PLAYBACK_RATE / BAUD_RATE + 0.5f)

// Fixed point arithmentic on the stride length through the sin wave table
// Note, the bottom "FIXED_PNT_BITS" bits of the counter are the fractional part
#define FIXED_PNT_BITS 6
#define FIXED_PNT_SCALE (1 << FIXED_PNT_BITS)

// The stride rates below are how much to add to the index through the sin table
// for each interrupt call
#define SAMPLE_STRIDE_TONE_FLOAT ((float)SAMPLES_PER_CYCLE * TONE_FREQUENCY / PLAYBACK_RATE)
#define SAMPLE_STRIDE_TONE_FIXED_PNT ((uint16_t)(SAMPLE_STRIDE_TONE_FLOAT * (float)FIXED_PNT_SCALE + 0.5f))

#define SAMPLE_STRIDE_MARK_FLOAT ((float)SAMPLES_PER_CYCLE * MARK_FREQUENCY / PLAYBACK_RATE)
#define SAMPLE_STRIDE_MARK_FIXED_PNT ((uint16_t)(SAMPLE_STRIDE_MARK_FLOAT * (float)FIXED_PNT_SCALE + 0.5f))

#define SAMPLE_STRIDE_SPACE_FLOAT ((float)SAMPLES_PER_CYCLE * SPACE_FREQUENCY / PLAYBACK_RATE)
#define SAMPLE_STRIDE_SPACE_FIXED_PNT ((uint16_t)(SAMPLE_STRIDE_SPACE_FLOAT * (float)FIXED_PNT_SCALE + 0.5f))

// The scale of the second sin table
#define TABLE2_SCALE 1.0f

// Store only 1/4th of a sin wave (plus one byte) to save progmem space.
// afsk_read_sample() does the math for the other 3/4ths.
const uint16_t afsk_sine_table1[129] = { 2047, 2072, 2097, 2122, 2147, 2173,
    2198, 2223, 2248, 2273, 2298, 2323, 2348, 2372, 2397, 2422, 2447, 2471,
    2496, 2520, 2545, 2569, 2593, 2617, 2642, 2666, 2689, 2713, 2737, 2761,
    2784, 2807, 2831, 2854, 2877, 2900, 2923, 2945, 2968, 2990, 3012, 3035,
    3056, 3078, 3100, 3121, 3143, 3164, 3185, 3206, 3226, 3247, 3267, 3287,
    3307, 3327, 3346, 3366, 3385, 3404, 3422, 3441, 3459, 3477, 3495, 3513,
    3530, 3547, 3564, 3581, 3598, 3614, 3630, 3646, 3662, 3677, 3692, 3707,
    3721, 3736, 3750, 3764, 3777, 3791, 3804, 3816, 3829, 3841, 3853, 3865,
    3876, 3887, 3898, 3909, 3919, 3929, 3939, 3949, 3958, 3967, 3975, 3984,
    3992, 3999, 4007, 4014, 4021, 4027, 4034, 4040, 4045, 4051, 4056, 4060,
    4065, 4069, 4073, 4076, 4080, 4083, 4085, 4087, 4089, 4091, 4093, 4094,
    4094, 4095, 4095, };

#define SINSCALE(x)     (uint16_t)((((float)(x)-2047.0f) * TABLE2_SCALE) + 2047.49f)

// After noticing on the oscilloscope that one of the frequency signals come accross at
// higher aplitutde than the others, I added the ability to have two sine-wave tables,
// one a scale from the other. The scale (TABLE2_SCALE) was should be determined experimentally.
const uint16_t afsk_sine_table2[129] = { SINSCALE(2047), SINSCALE(2072),
    SINSCALE(2097), SINSCALE(2122), SINSCALE(2147), SINSCALE(2173), SINSCALE(
        2198), SINSCALE(2223), SINSCALE(2248), SINSCALE(2273), SINSCALE(2298),
    SINSCALE(2323), SINSCALE(2348), SINSCALE(2372), SINSCALE(2397), SINSCALE(
        2422), SINSCALE(2447), SINSCALE(2471), SINSCALE(2496), SINSCALE(2520),
    SINSCALE(2545), SINSCALE(2569), SINSCALE(2593), SINSCALE(2617), SINSCALE(
        2642), SINSCALE(2666), SINSCALE(2689), SINSCALE(2713), SINSCALE(2737),
    SINSCALE(2761), SINSCALE(2784), SINSCALE(2807), SINSCALE(2831), SINSCALE(
        2854), SINSCALE(2877), SINSCALE(2900), SINSCALE(2923), SINSCALE(2945),
    SINSCALE(2968), SINSCALE(2990), SINSCALE(3012), SINSCALE(3035), SINSCALE(
        3056), SINSCALE(3078), SINSCALE(3100), SINSCALE(3121), SINSCALE(3143),
    SINSCALE(3164), SINSCALE(3185), SINSCALE(3206), SINSCALE(3226), SINSCALE(
        3247), SINSCALE(3267), SINSCALE(3287), SINSCALE(3307), SINSCALE(3327),
    SINSCALE(3346), SINSCALE(3366), SINSCALE(3385), SINSCALE(3404), SINSCALE(
        3422), SINSCALE(3441), SINSCALE(3459), SINSCALE(3477), SINSCALE(3495),
    SINSCALE(3513), SINSCALE(3530), SINSCALE(3547), SINSCALE(3564), SINSCALE(
        3581), SINSCALE(3598), SINSCALE(3614), SINSCALE(3630), SINSCALE(3646),
    SINSCALE(3662), SINSCALE(3677), SINSCALE(3692), SINSCALE(3707), SINSCALE(
        3721), SINSCALE(3736), SINSCALE(3750), SINSCALE(3764), SINSCALE(3777),
    SINSCALE(3791), SINSCALE(3804), SINSCALE(3816), SINSCALE(3829), SINSCALE(
        3841), SINSCALE(3853), SINSCALE(3865), SINSCALE(3876), SINSCALE(3887),
    SINSCALE(3898), SINSCALE(3909), SINSCALE(3919), SINSCALE(3929), SINSCALE(
        3939), SINSCALE(3949), SINSCALE(3958), SINSCALE(3967), SINSCALE(3975),
    SINSCALE(3984), SINSCALE(3992), SINSCALE(3999), SINSCALE(4007), SINSCALE(
        4014), SINSCALE(4021), SINSCALE(4027), SINSCALE(4034), SINSCALE(4040),
    SINSCALE(4045), SINSCALE(4051), SINSCALE(4056), SINSCALE(4060), SINSCALE(
        4065), SINSCALE(4069), SINSCALE(4073), SINSCALE(4076), SINSCALE(4080),
    SINSCALE(4083), SINSCALE(4085), SINSCALE(4087), SINSCALE(4089), SINSCALE(
        4091), SINSCALE(4093), SINSCALE(4094), SINSCALE(4094), SINSCALE(4095),
    SINSCALE(4095),

};

// We keep potentially 2 different tables for the two frequencies.
// The idea has to do with the complications of pre-emphasis if this signal
// is put on the microphone input of a radio that tries to amplify
// the higher frequencies to get a better SNR. Read about it here:
// http://en.wikipedia.org/wiki/Preemphasis_improvement
#define SIN_TABLE_MARK afsk_sine_table2
#define SIN_TABLE_SPACE afsk_sine_table1

// Module globals
volatile bool busy = false;                         // Modem is on

static const uint16_t *afsk_sine_table; // The sin table we are going through
static uint32_t sine_table_switcher; // The bit mask to switch sin tables quick

static uint32_t currentSampleCount; // How many output sample have been sent for the current bit
static uint16_t currentStride;    // 1200/2200 for standard AX.25
static uint16_t currentSample;           // Fixed point 
static uint32_t totalSamplesSent;
static uint8_t current_byte = 0;

// Buffer of bytes to send
static const uint8_t *afsk_packet;
static uint32_t afsk_packet_size = 0; // How many bytes in the packet
static uint32_t packet_pos;       // Next bit to be sent out 

static bool fDoTone;
static uint32_t toneStop, silenceStop;
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

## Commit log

2017-02-04 Add pinmap
    [pinmap.csv]
2017-02-05 Fix HX1 pin table
2017-02-15 Add KiCAD project, Teensy lib
    [BalloonPCB.kicad_pcb, BalloonPCB.sch]
2017-02-24 Change to Arduino file type
2017-03-11 Started PCB layout
    [BalloonPCB.kicad_pcb, BalloonPCB.sch]
2017-03-11 First routing pass, everything except radio
    [BalloonPCB.kicad_pcb, BalloonPCB.sch]
2017-03-11 PCB signals routed
    [BalloonPCB.kicad_pcb, BalloonPCB.sch]
2017-03-18 Board fully routed, add decoupling caps
    [BalloonPCB.kicad_pcb, BalloonPCB.sch]
2017-03-18 Add pours
    [BalloonPCB.kicad_pcb, BalloonPCB.sch]
2017-03-19 Add spot for thermristor
    [BalloonPCB.kicad_pcb, BalloonPCB.sch]
2017-03-20 Add prototyping section
    [BalloonPCB.kicad_pcb, BalloonPCB.sch]
2017-03-20 First revision export
    [BalloonPCB.kicad_pcb, BalloonPCB.sch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]
2017-03-20 Update to reflect PCB
2017-03-20 Update pin configuration documentation
    [pinmap.csv]
2017-03-20 Change to pull tx enable pin low on start
2017-03-20 Many typo and type fixes, code now compiles
    [HAB.ino, aprs.cpp]
2017-03-24 Fix serial baud rates
    [GPS_SerialDebug.ino, HAB.ino]
2017-03-24 Command formats exported from u-central
    [ublox_config.txt]
2017-04-11 Field trials, fix PTT pin number, still debugging ublox code
    [HAB.ino, afsk.cpp, ublox.cpp]
2017-04-15 Fixed Ublox config, add DAC output recordings
    [HAB.ino, UBloxExample.ino, aprs.cpp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]
2017-04-15 Add BMP180 code, rename TinyGPS to fix IDE detect
    [HAB.ino, aprs.cpp, bmp180test.ino]
2017-04-15 Add thermistor code
2017-04-16 Add GPS mode switching based on altitude (untested)
2017-04-16 Live test result
    [DATA.CSV]
2017-04-27 Add Antenna Board design
    [AntennaBoards.kicad_pcb, AntennaBoards.sch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]
2017-05-17 Fix longitude/latitude conversion bug
    [HAB.ino, aprs.cpp]
2017-10-18 Add board photos
2017-12-06 Add data from flight
    [aprsfi_export_AG6GR-11_20171130_182320_20171202_182320.csv, aprsfi_export_AG6GR-11_20171130_182320_20171202_182320.xlsx, flight_path.csv]

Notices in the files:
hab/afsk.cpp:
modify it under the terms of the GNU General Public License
